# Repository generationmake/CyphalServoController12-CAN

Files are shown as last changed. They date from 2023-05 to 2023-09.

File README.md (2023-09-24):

# CyphalServoController12/CAN
Board to control up to 12 servos with a Raspberry Pi Pico to connect via CAN using OpenCyphal and UCANPHY Micro

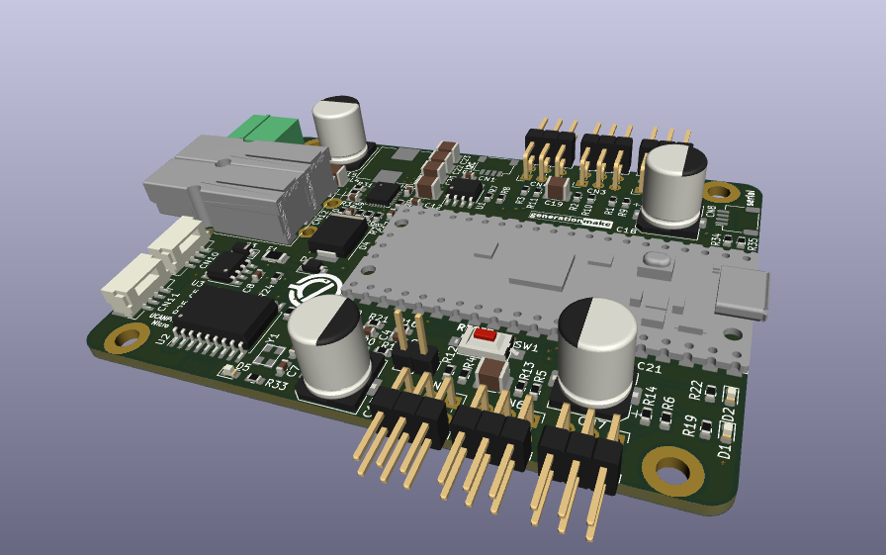
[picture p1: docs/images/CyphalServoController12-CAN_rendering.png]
CyphalServoController12/CAN rendering


## Description

### analog measurements

| **channel** | **usage** | **range**  |
|:---:|:---:|:---:|
| ADC0 | battery voltage | 0 - 66 V |
| ADC1 | servo voltage | 0 - 6.6 V  |
| ADC2 | CAN bus voltage | 0 - 6.6 V  |

### power supply

The power for the microcontroller and the CAN interface can be fed via the CAN connector or thepower regulator for the servos. The power regulator for the servos can be enabled and disabled by the microcontroller to save power in stand-by.

input voltage: 10 - 40 V

## PCB

### Top

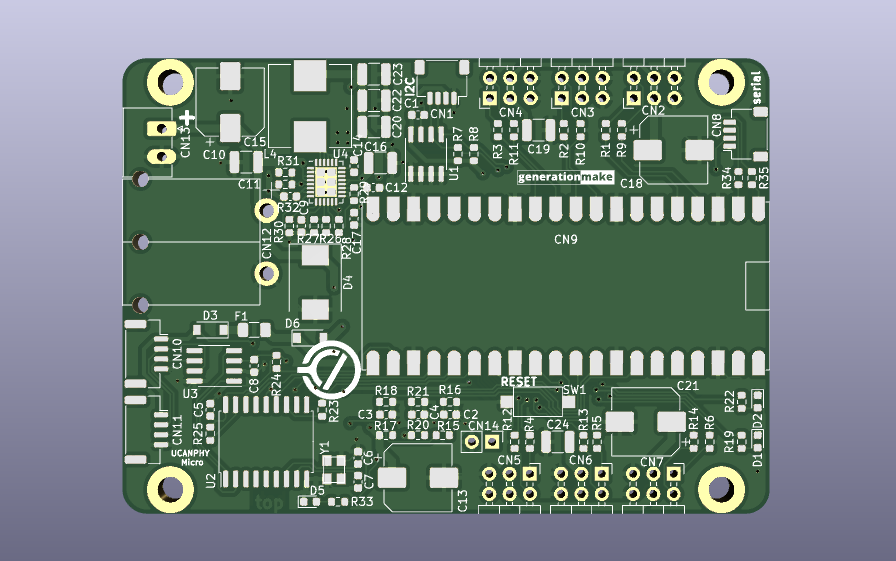
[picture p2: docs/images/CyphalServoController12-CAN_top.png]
CyphalServoController12/CAN PCB top


### Bottom

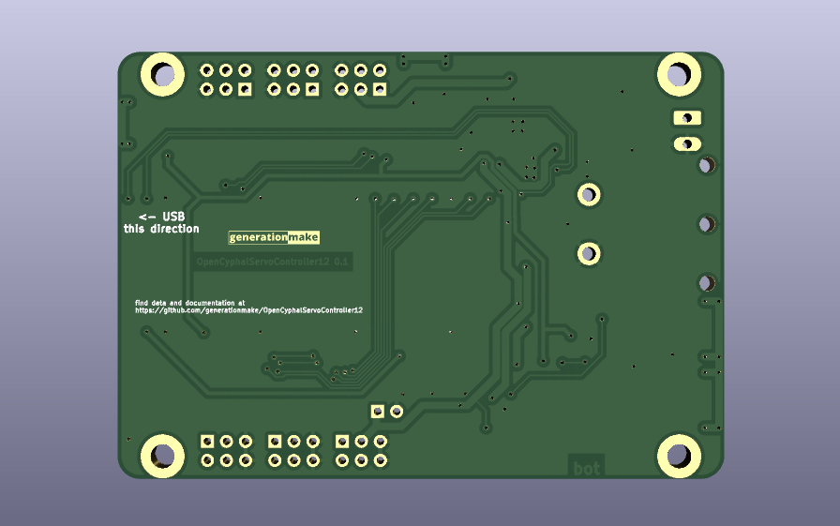
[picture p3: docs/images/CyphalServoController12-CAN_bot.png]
CyphalServoController12/CAN PCB bot


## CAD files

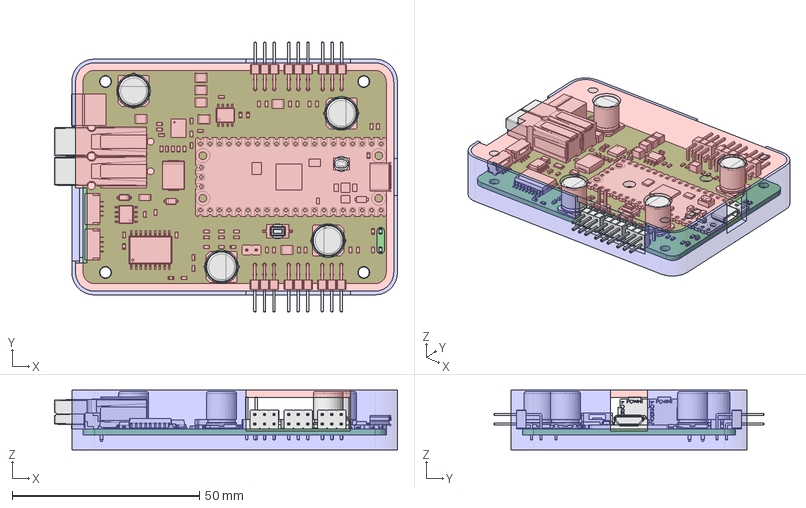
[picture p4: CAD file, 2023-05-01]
freecad_source/enclosure.FCStd
91.6 x 72.2 x 16.0 mm
bottom
top
OpenCyphalServoController12 PCB

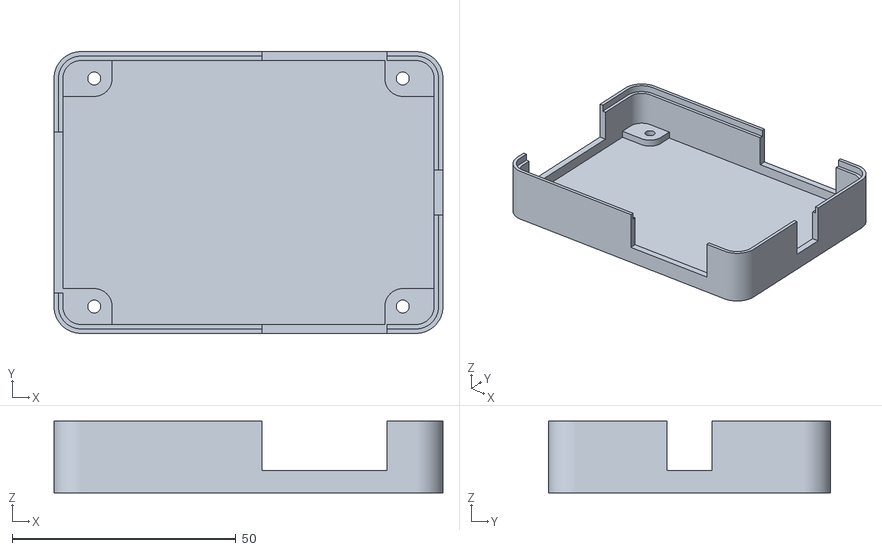
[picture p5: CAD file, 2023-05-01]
production_data/enclosure-bottom.stl
87.0 x 63.0 x 16.0

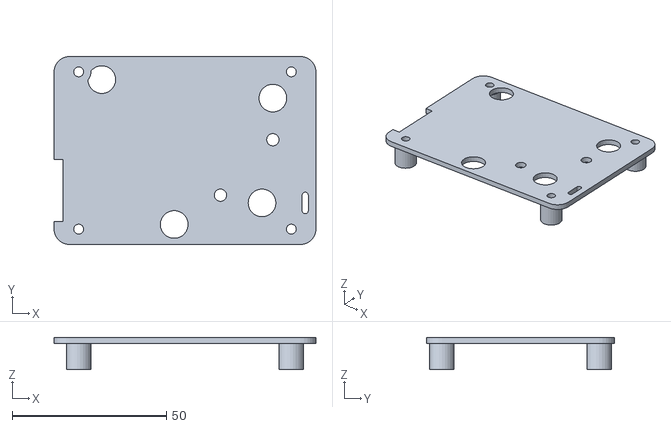
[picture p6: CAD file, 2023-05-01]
production_data/enclosure-top.stl
85.0 x 61.0 x 10.4

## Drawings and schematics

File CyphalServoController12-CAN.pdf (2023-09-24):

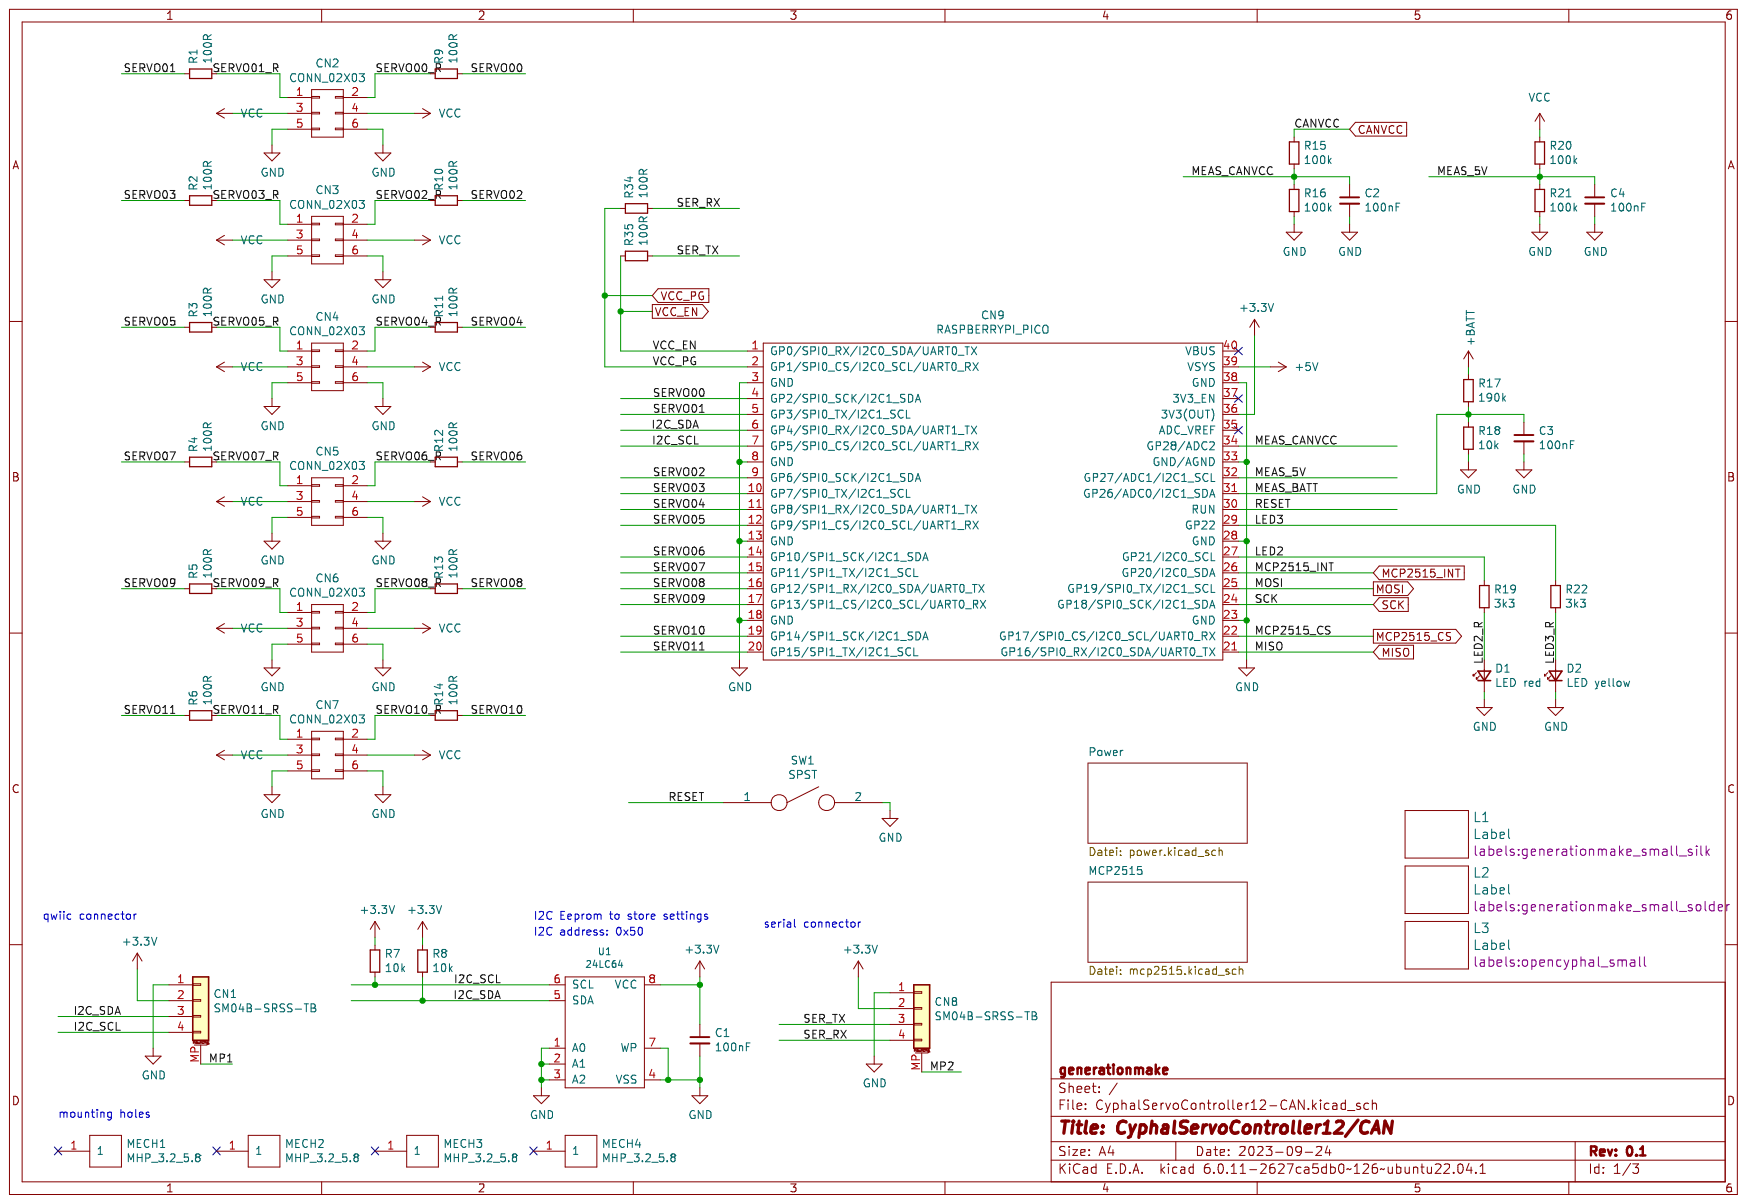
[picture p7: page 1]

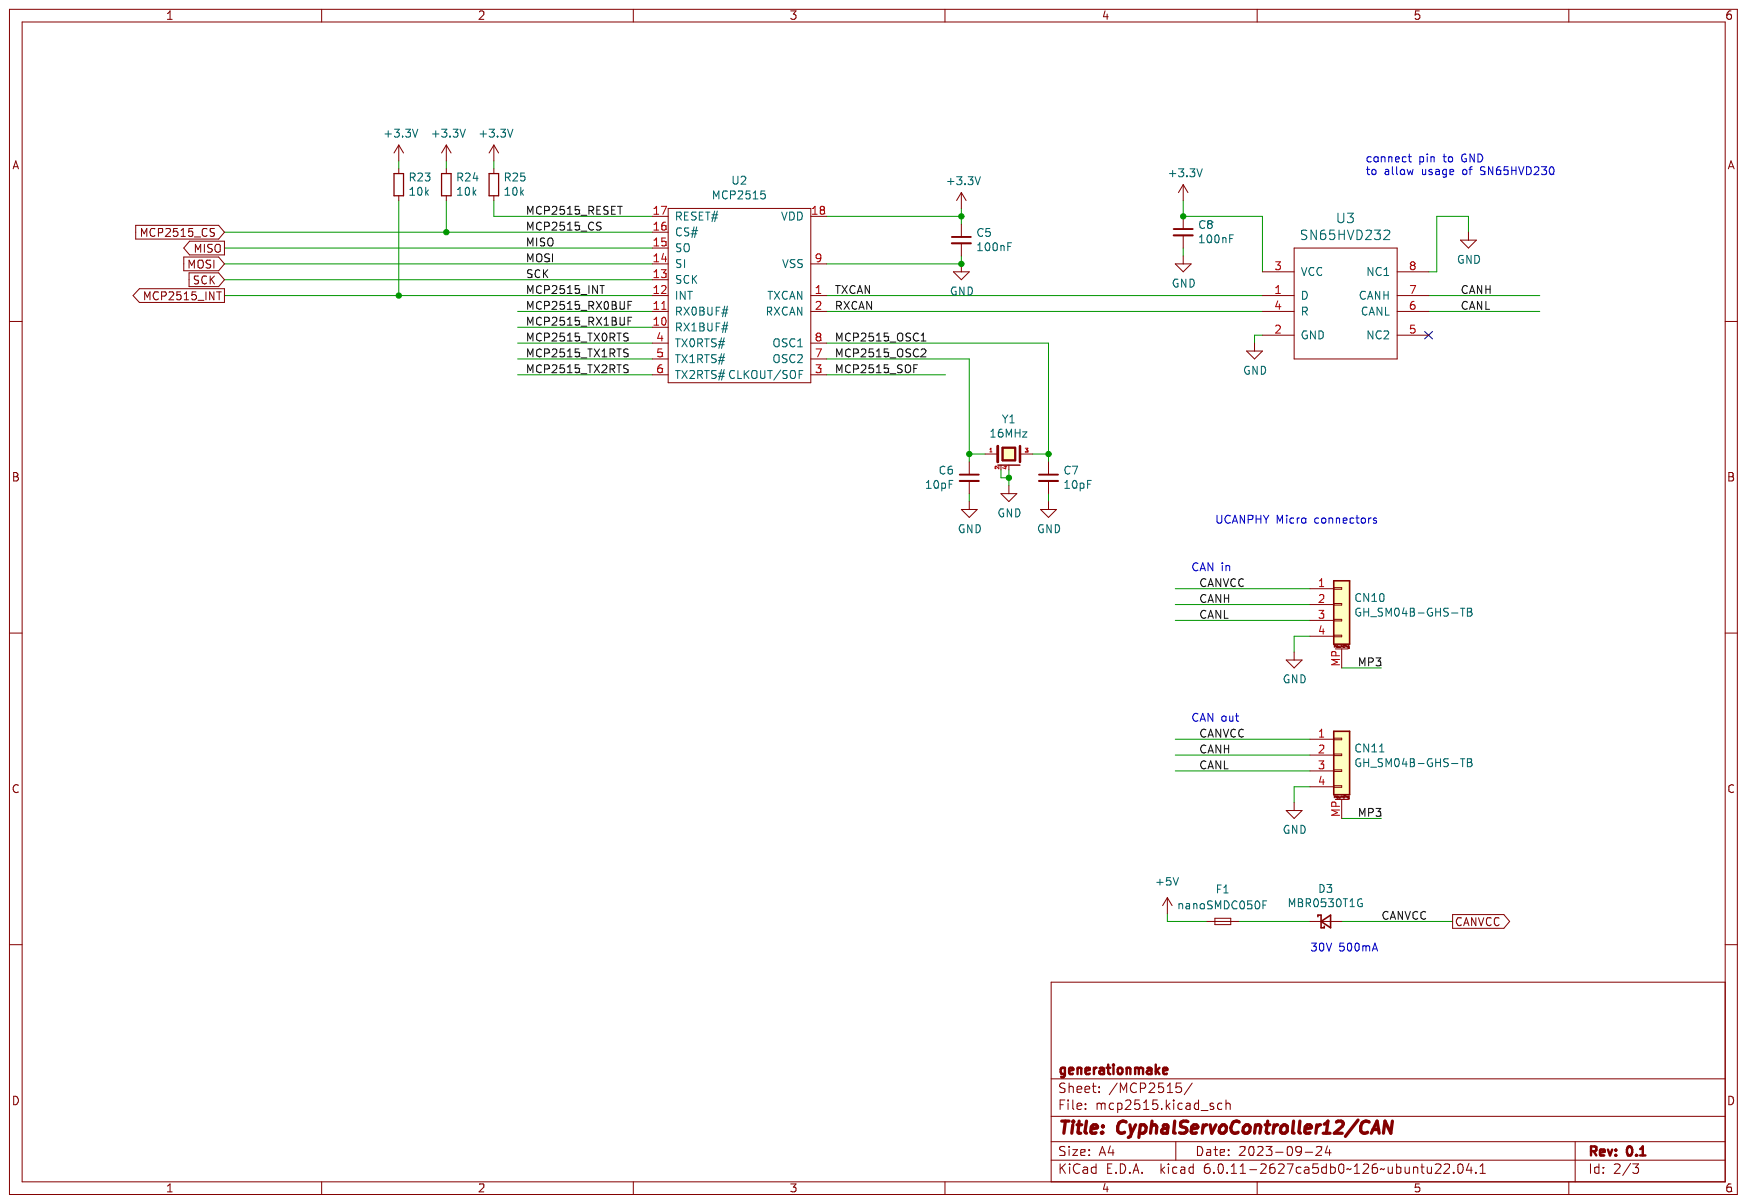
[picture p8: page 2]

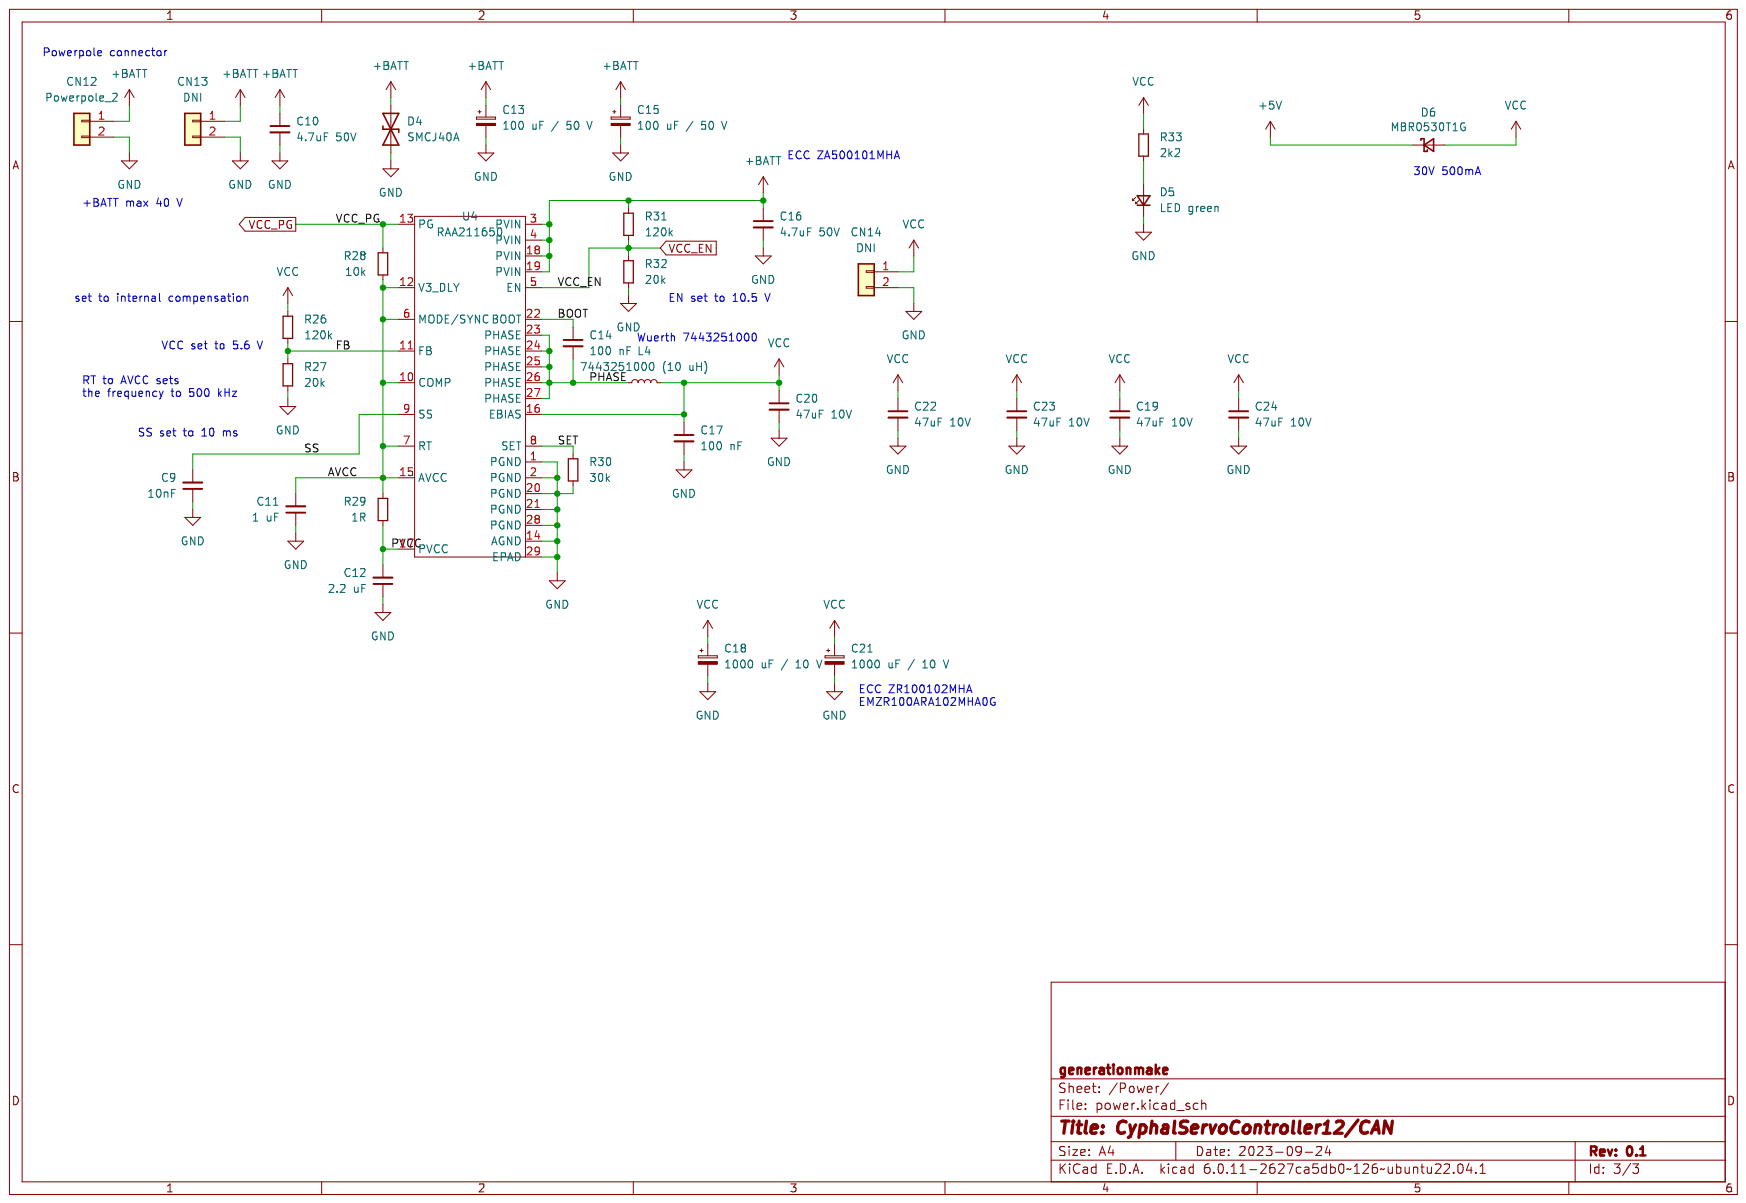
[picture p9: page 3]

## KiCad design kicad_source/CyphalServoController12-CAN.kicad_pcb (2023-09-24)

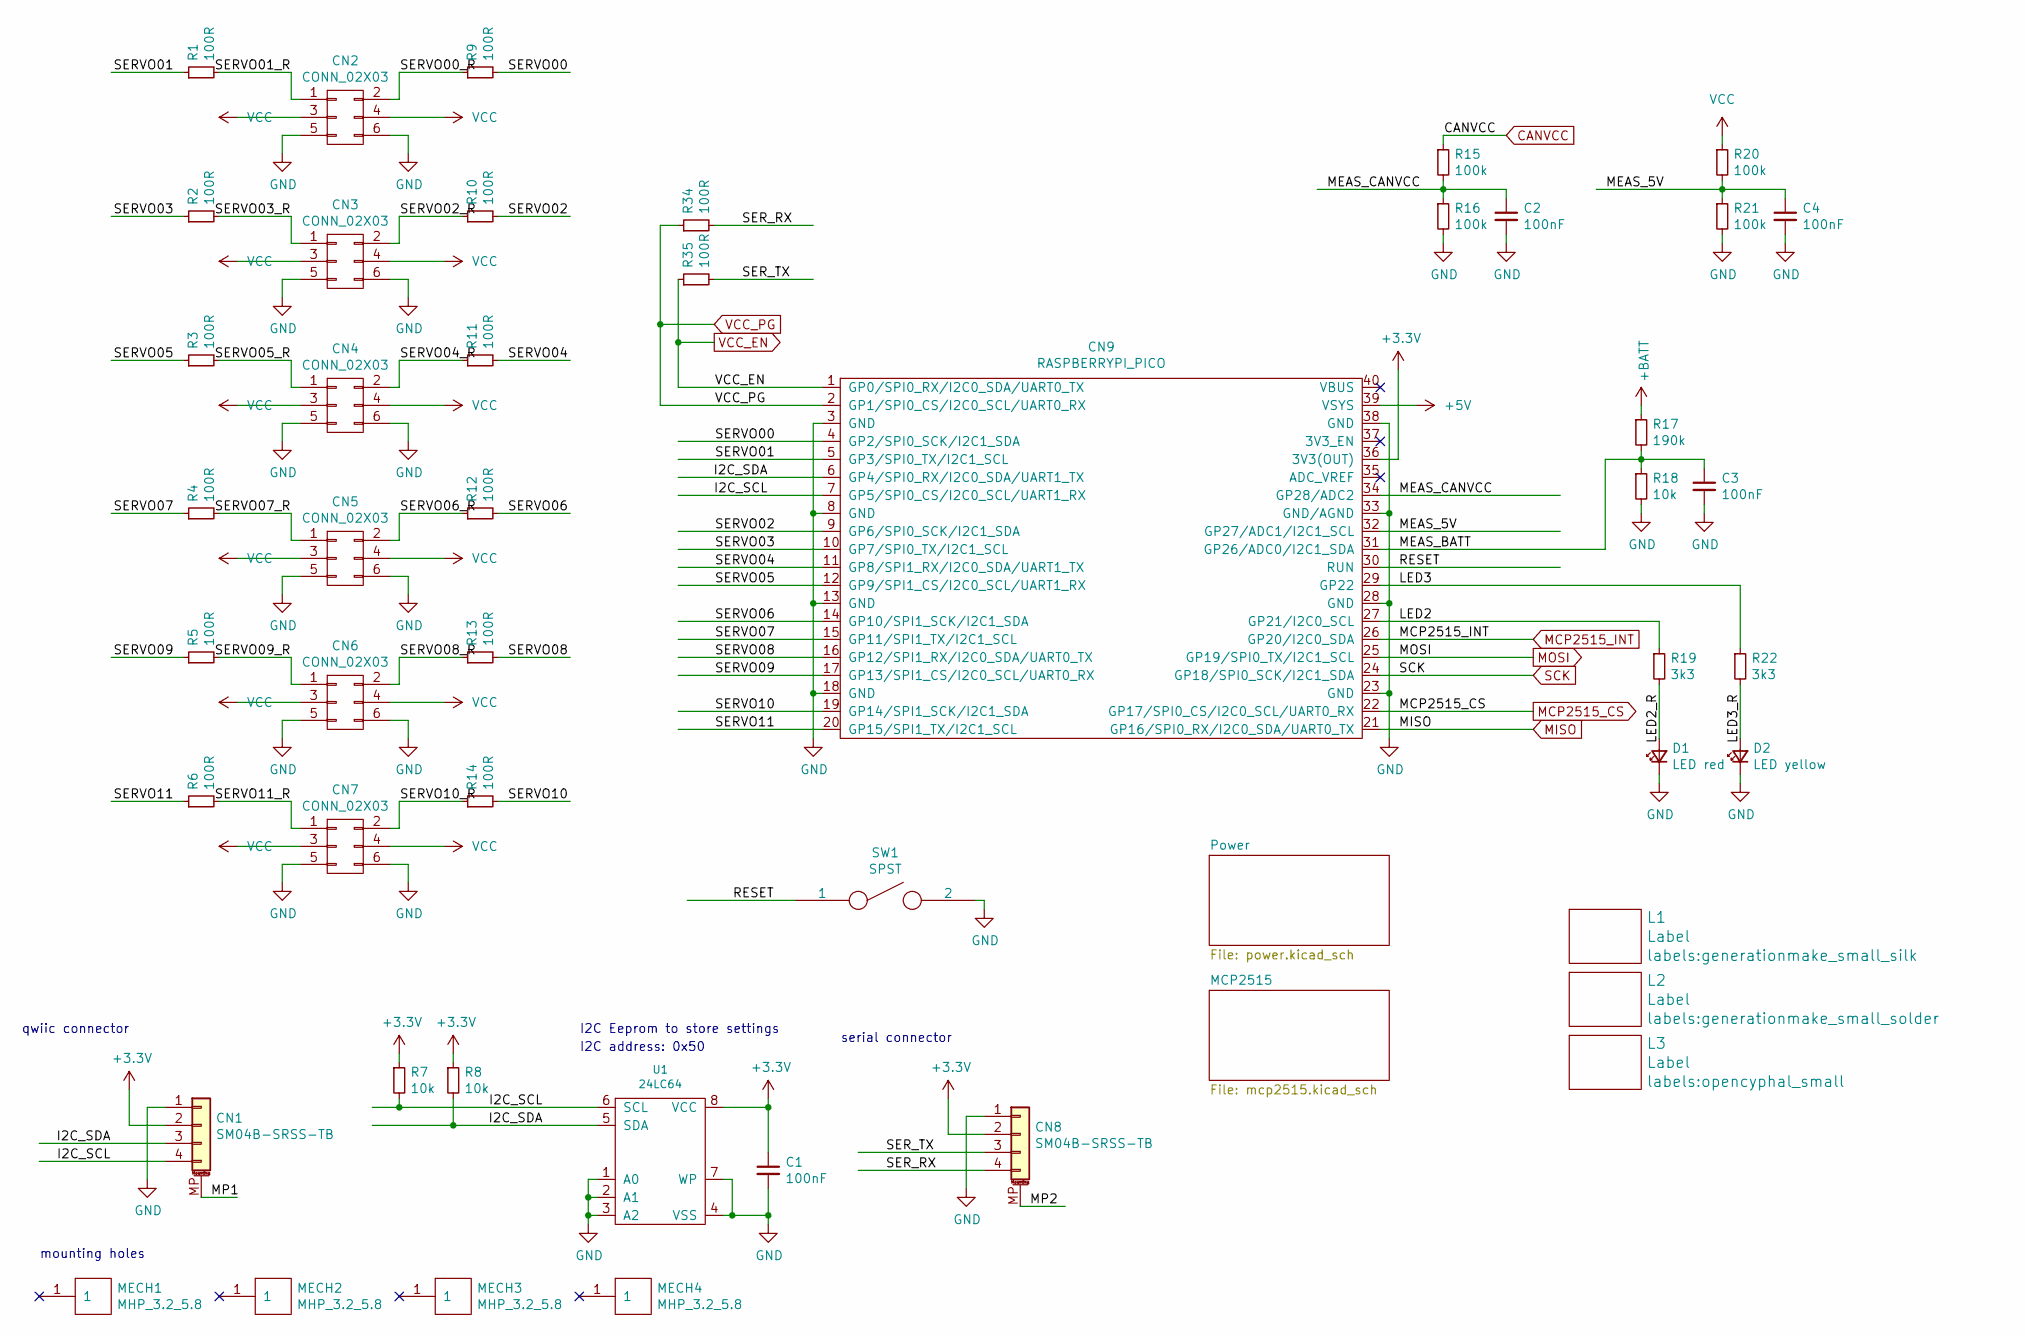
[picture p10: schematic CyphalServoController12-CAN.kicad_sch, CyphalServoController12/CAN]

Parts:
C1, C2, C3, C4: 100nF; C_0603_1608Metric
CN1, CN8: SM04B-SRSS-TB; JST_SH_SM04B-SRSS-TB_1x04-1MP_P1.00mm_Horizontal
CN2, CN3, CN4, CN5, CN6, CN7: CONN_02X03; PinHeader_2x03_P2.54mm_Horizontal
CN9: RASPBERRYPI_PICO; RASPI_PICO_SOLDER_Kopie
D1: LED red; LED_0603_1608Metric
D2: LED yellow; LED_0603_1608Metric
L1: Label; generationmake_small_silk
L2: Label; generationmake_small_solder
L3: Label; opencyphal_small
MECH1, MECH2, MECH3, MECH4: MHP_3.2_5.8
R1, R2, R3, R4, R5, R6, R9, R10, R11, R12, R13, R14, R34, R35: 100R; R_0603_1608Metric
R7, R8, R18: 10k; R_0603_1608Metric
R15, R16, R20, R21: 100k; R_0603_1608Metric
R17: 190k; R_0603_1608Metric
R19, R22: 3k3; R_0603_1608Metric
SW1: SPST; SW_SPST_CK_RS282G05A3
U1: 24LC64; SOIC-8_3.9x4.9mm_P1.27mm

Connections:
+3V3: C1.1, CN1.2, CN8.2, CN9.36 (3V3(OUT)), R7.1, R8.1, U1.8 (VCC); also elsewhere on the board
+5V: CN9.39 (VSYS); also elsewhere on the board
+BATT: R17.1; also elsewhere on the board
/I2C_SCL: CN1.4, CN9.7 (GP5/SPI0_CS/I2C0_SCL/UART1_RX), R7.2, U1.6 (SCL)
/I2C_SDA: CN1.3, CN9.6 (GP4/SPI0_RX/I2C0_SDA/UART1_TX), R8.2, U1.5 (SDA)
/LED2: CN9.27 (GP21/I2C0_SCL), R19.1
/LED2_R: D1.2 (A), R19.2
/LED3: CN9.29 (GP22), R22.1
/LED3_R: D2.2 (A), R22.2
/MEAS_5V: C4.1, CN9.32 (GP27/ADC1/I2C1_SCL), R20.2, R21.1
/MEAS_BATT: C3.1, CN9.31 (GP26/ADC0/I2C1_SDA), R17.2, R18.1
/MEAS_CANVCC: C2.1, CN9.34 (GP28/ADC2), R15.2, R16.1
/MP1: CN1.MP (MountPin)
/MP2: CN8.MP (MountPin)
/RESET: CN9.30 (RUN), SW1.1
/SERVO00: CN9.4 (GP2/SPI0_SCK/I2C1_SDA), R9.2
/SERVO00_R: CN2.2, R9.1
/SERVO01: CN9.5 (GP3/SPI0_TX/I2C1_SCL), R1.1
/SERVO01_R: CN2.1, R1.2
/SERVO02: CN9.9 (GP6/SPI0_SCK/I2C1_SDA), R10.2
/SERVO02_R: CN3.2, R10.1
/SERVO03: CN9.10 (GP7/SPI0_TX/I2C1_SCL), R2.1
/SERVO03_R: CN3.1, R2.2
/SERVO04: CN9.11 (GP8/SPI1_RX/I2C0_SDA/UART1_TX), R11.2
/SERVO04_R: CN4.2, R11.1
/SERVO05: CN9.12 (GP9/SPI1_CS/I2C0_SCL/UART1_RX), R3.1
/SERVO05_R: CN4.1, R3.2
/SERVO06: CN9.14 (GP10/SPI1_SCK/I2C1_SDA), R12.2
/SERVO06_R: CN5.2, R12.1
/SERVO07: CN9.15 (GP11/SPI1_TX/I2C1_SCL), R4.1
/SERVO07_R: CN5.1, R4.2
/SERVO08: CN9.16 (GP12/SPI1_RX/I2C0_SDA/UART0_TX), R13.2
/SERVO08_R: CN6.2, R13.1
/SERVO09: CN9.17 (GP13/SPI1_CS/I2C0_SCL/UART0_RX), R5.1
/SERVO09_R: CN6.1, R5.2
/SERVO10: CN9.19 (GP14/SPI1_SCK/I2C1_SDA), R14.2
/SERVO10_R: CN7.2, R14.1
/SERVO11: CN9.20 (GP15/SPI1_TX/I2C1_SCL), R6.1
/SERVO11_R: CN7.1, R6.2
/SER_RX: CN8.4, R34.2
/SER_TX: CN8.3, R35.2
CANVCC: R15.1; also elsewhere on the board
GND: C1.2, C2.2, C3.2, C4.2, CN1.1, CN2.5, CN2.6, CN3.5, CN3.6, CN4.5, CN4.6, CN5.5, CN5.6, CN6.5, CN6.6, CN7.5, CN7.6, CN8.1, CN9.3 (GND), CN9.8 (GND), CN9.13 (GND), CN9.18 (GND), CN9.23 (GND), CN9.28 (GND), CN9.33 (GND/AGND), CN9.38 (GND), D1.1 (K), D2.1 (K), R16.2, R18.2, R21.2, SW1.2, U1.1 (A0), U1.2 (A1), U1.3 (A2), U1.4 (VSS), U1.7 (WP); also elsewhere on the board
MCP2515_CS: CN9.22 (GP17/SPI0_CS/I2C0_SCL/UART0_RX); also elsewhere on the board
MCP2515_INT: CN9.26 (GP20/I2C0_SDA); also elsewhere on the board
MISO: CN9.21 (GP16/SPI0_RX/I2C0_SDA/UART0_TX); also elsewhere on the board
MOSI: CN9.25 (GP19/SPI0_TX/I2C1_SCL); also elsewhere on the board
SCK: CN9.24 (GP18/SPI0_SCK/I2C1_SDA); also elsewhere on the board
VCC: CN2.3, CN2.4, CN3.3, CN3.4, CN4.3, CN4.4, CN5.3, CN5.4, CN6.3, CN6.4, CN7.3, CN7.4, R20.1; also elsewhere on the board
VCC_EN: CN9.1 (GP0/SPI0_RX/I2C0_SDA/UART0_TX), R35.1; also elsewhere on the board
VCC_PG: CN9.2 (GP1/SPI0_CS/I2C0_SCL/UART0_RX), R34.1; also elsewhere on the board

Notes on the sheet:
serial connector
qwiic connector
mounting holes
I2C address: 0x50
I2C Eeprom to store settings

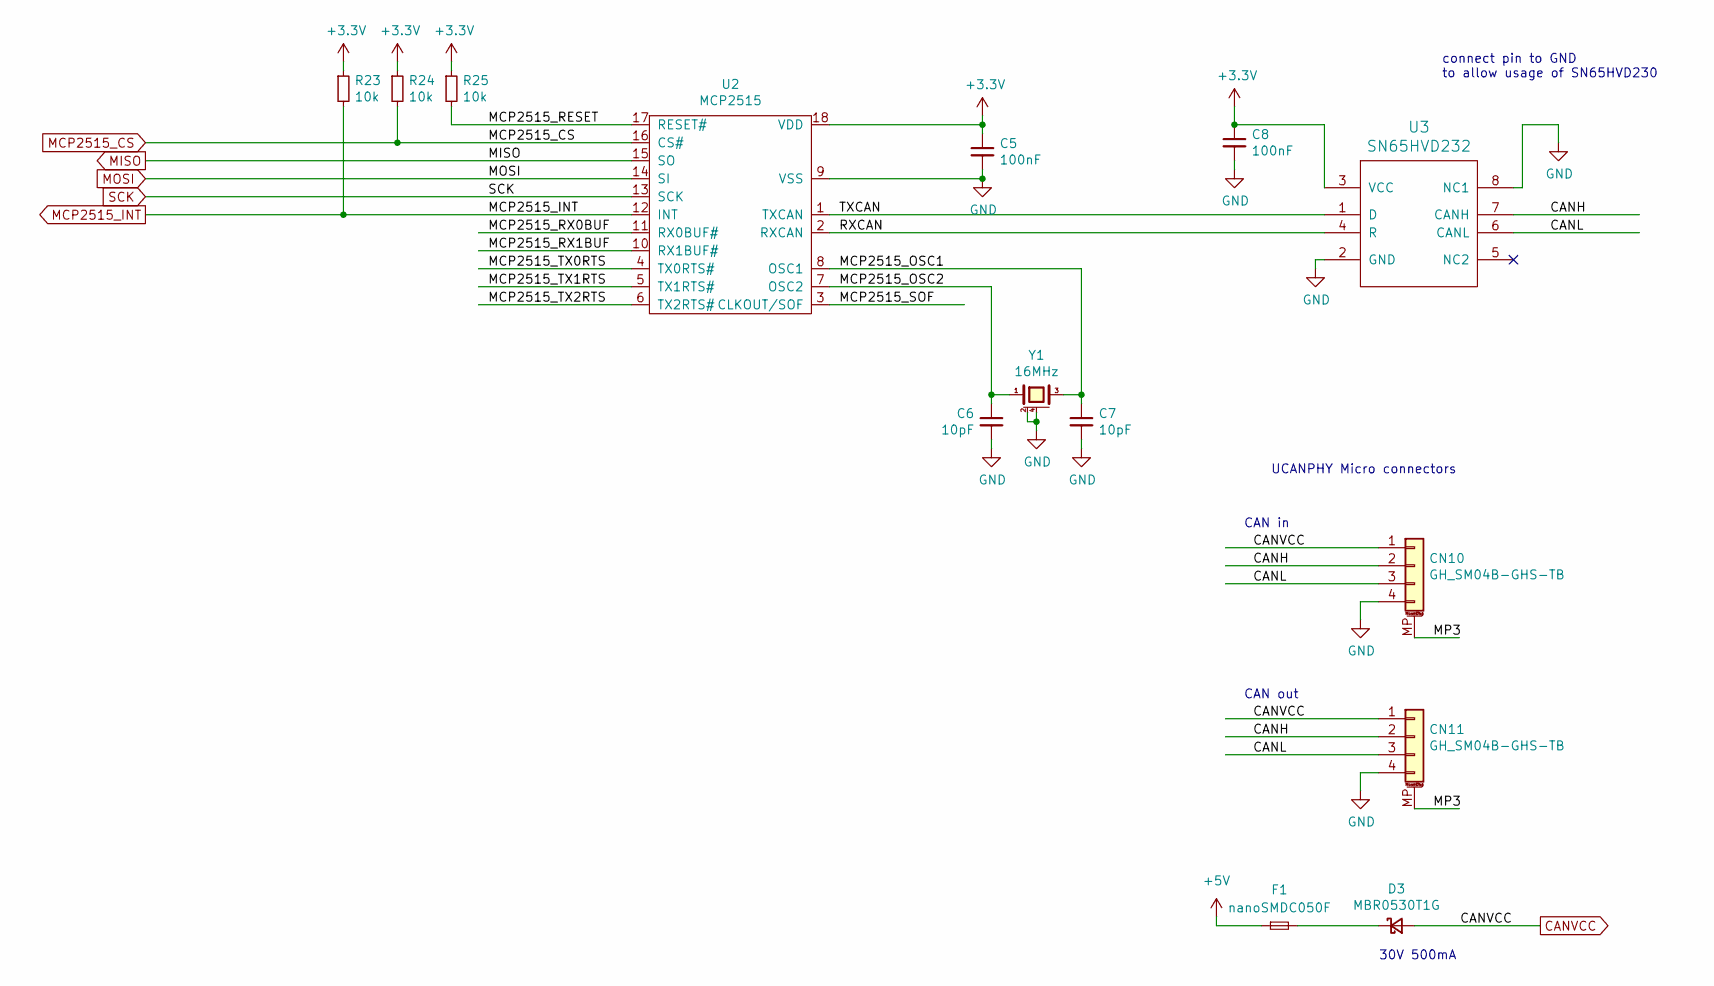
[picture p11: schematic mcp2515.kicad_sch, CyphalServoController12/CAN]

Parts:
C5, C8: 100nF; C_0603_1608Metric
C6, C7: 10pF; C_0603_1608Metric
CN10, CN11: GH_SM04B-GHS-TB; JST_GH_SM04B-GHS-TB_1x04-1MP_P1.25mm_Horizontal
D3: MBR0530T1G; D_SOD-123
F1: nanoSMDC050F; Fuse_1206_3216Metric
R23, R24, R25: 10k; R_0603_1608Metric
U2: MCP2515; SOIC-18W_7.5x11.6mm_P1.27mm
U3: SN65HVD232; SOIC-8_3.9x4.9mm_P1.27mm
Y1: 16MHz; Crystal_SMD_3.2x2.5mm_4Pad

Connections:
+3V3: C5.1, C8.1, R23.1, R24.1, R25.1, U2.18 (VDD), U3.3 (VCC); also elsewhere on the board
+5V: F1.1; also elsewhere on the board
/MCP2515/CANH: CN10.2, CN11.2, U3.7 (CANH)
/MCP2515/CANL: CN10.3, CN11.3, U3.6 (CANL)
/MCP2515/MCP2515_OSC1: C7.1, U2.8 (OSC1), Y1.3
/MCP2515/MCP2515_OSC2: C6.1, U2.7 (OSC2), Y1.1
/MCP2515/MCP2515_RESET: R25.2, U2.17 (RESET#)
/MCP2515/MCP2515_RX0BUF: U2.11 (RX0BUF#)
/MCP2515/MCP2515_RX1BUF: U2.10 (RX1BUF#)
/MCP2515/MCP2515_SOF: U2.3 (CLKOUT/SOF)
/MCP2515/MCP2515_TX0RTS: U2.4 (TX0RTS#)
/MCP2515/MCP2515_TX1RTS: U2.5 (TX1RTS#)
/MCP2515/MCP2515_TX2RTS: U2.6 (TX2RTS#)
/MCP2515/MP3: CN10.MP (MountPin), CN11.MP (MountPin)
/MCP2515/RXCAN: U2.2 (RXCAN), U3.4 (R)
/MCP2515/TXCAN: U2.1 (TXCAN), U3.1 (D)
CANVCC: CN10.1, CN11.1, D3.2 (A); also elsewhere on the board
GND: C5.2, C6.2, C7.2, C8.2, CN10.4, CN11.4, U2.9 (VSS), U3.2 (GND), U3.8 (NC1), Y1.2 (case), Y1.4 (case); also elsewhere on the board
MCP2515_CS: R24.2, U2.16 (CS#); also elsewhere on the board
MCP2515_INT: R23.2, U2.12 (INT); also elsewhere on the board
MISO: U2.15 (SO); also elsewhere on the board
MOSI: U2.14 (SI); also elsewhere on the board
unnamed: D3.1 (K), F1.2
SCK: U2.13 (SCK); also elsewhere on the board

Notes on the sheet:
connect pin to GND to allow usage of SN65HVD230
UCANPHY Micro connectors
30V 500mA
CAN in
CAN out

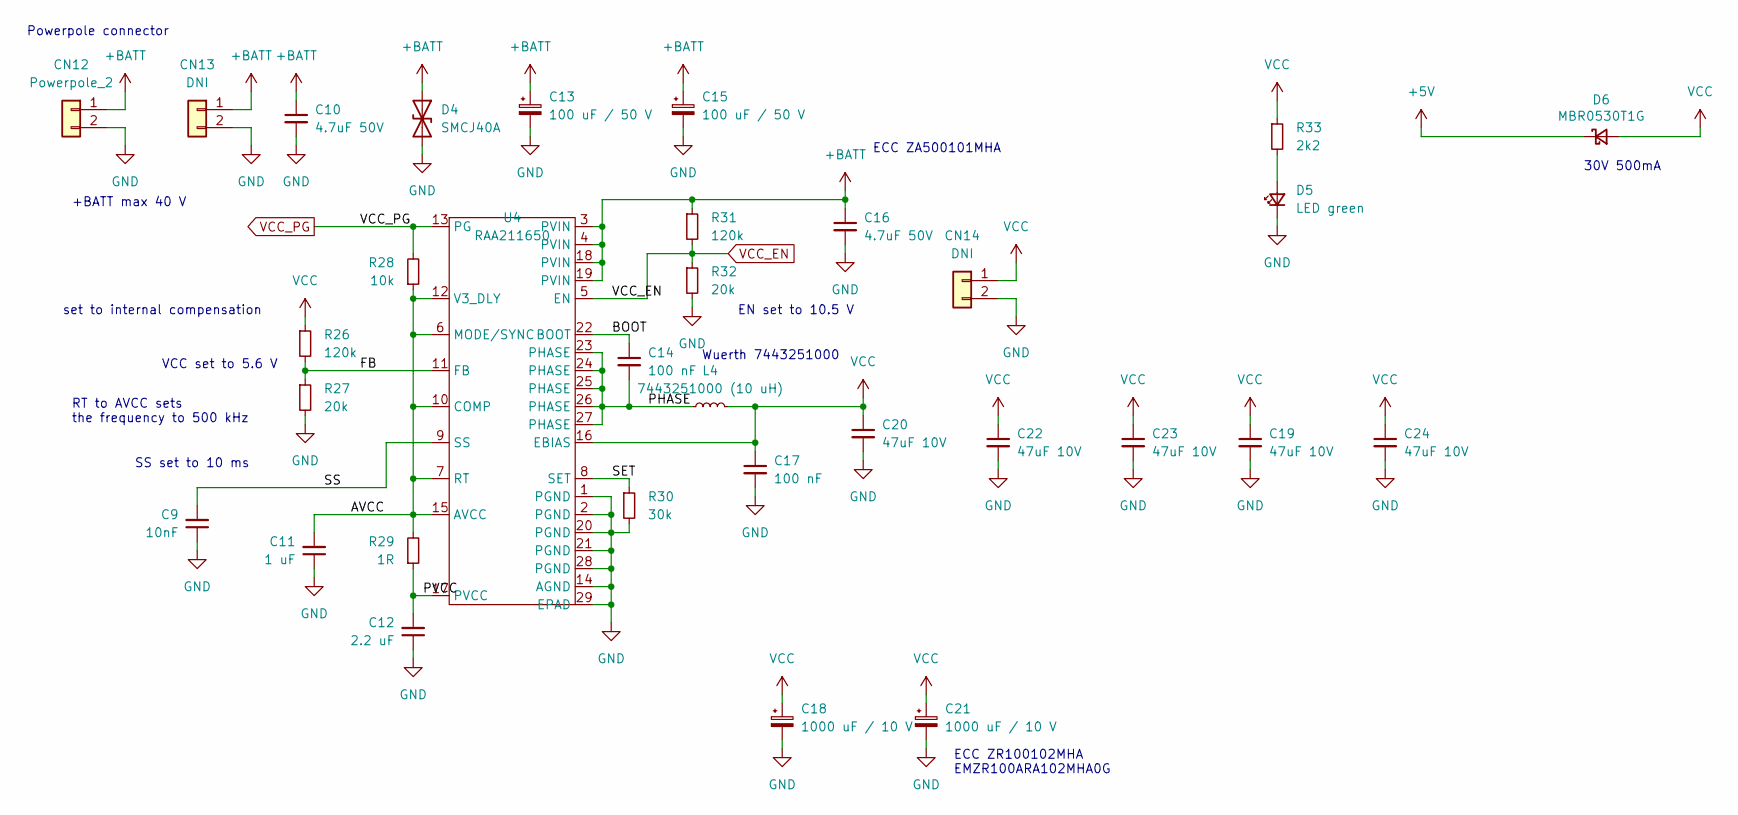
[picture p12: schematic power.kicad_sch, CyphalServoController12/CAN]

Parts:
C9: 10nF; C_0603_1608Metric
C10, C16: 4.7uF 50V; C_1210_3225Metric
C11: 1 uF; C_0603_1608Metric
C12: 2.2 uF; C_0603_1608Metric
C13, C15: 100 uF / 50 V; CP_Elec_8x10
C14, C17: 100 nF; C_0603_1608Metric
C18, C21: 1000 uF / 10 V; CP_Elec_8x10
C19, C20, C22, C23, C24: 47uF 10V; C_1210_3225Metric
CN12: Powerpole_2; POWERPOLE_hor_2
CN13: DNI; PhoenixContact_MC_1,5_2-G-3.5_1x02_P3.50mm_Horizontal
CN14: DNI; PinHeader_1x02_P2.54mm_Vertical
D4: SMCJ40A; D_SMC
D5: LED green; LED_0603_1608Metric
D6: MBR0530T1G; D_SOD-123
L4: 7443251000 (10 uH); L_Wuerth_HCI-1050
R26, R31: 120k; R_0603_1608Metric
R27, R32: 20k; R_0603_1608Metric
R28: 10k; R_0603_1608Metric
R29: 1R; R_0603_1608Metric
R30: 30k; R_0603_1608Metric
R33: 2k2; R_0603_1608Metric
U4: RAA211650; QFN-28-1EP_4x5mm_P0.5mm_EP2.65x3.65mm

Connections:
+5V: D6.1 (K); also elsewhere on the board
+BATT: C10.1, C13.1, C15.1, C16.1, CN12.1, CN13.1, D4.1 (A1), R31.1, U4.3 (PVIN), U4.4 (PVIN), U4.18 (PVIN), U4.19 (PVIN); also elsewhere on the board
/Power/AVCC: C11.2, R28.1, R29.2, U4.6 (MODE/SYNC), U4.7 (RT), U4.10 (COMP), U4.12 (V3_DLY), U4.15 (AVCC)
/Power/BOOT: C14.1, U4.22 (BOOT)
/Power/FB: R26.2, R27.1, U4.11 (FB)
/Power/PHASE: C14.2, L4.1, U4.23 (PHASE), U4.24 (PHASE), U4.25 (PHASE), U4.26 (PHASE), U4.27 (PHASE)
/Power/PVCC: C12.2, R29.1, U4.17 (PVCC)
/Power/SET: R30.1, U4.8 (SET)
/Power/SS: C9.2, U4.9 (SS)
GND: C9.1, C10.2, C11.1, C12.1, C13.2, C15.2, C16.2, C17.2, C18.2, C19.2, C20.2, C21.2, C22.2, C23.2, C24.2, CN12.2, CN13.2, CN14.2, D4.2 (A2), D5.1 (K), R27.2, R30.2, R32.2, U4.1 (PGND), U4.2 (PGND), U4.14 (AGND), U4.20 (PGND), U4.21 (PGND), U4.28 (PGND), U4.29 (EPAD); also elsewhere on the board
unnamed: D5.2 (A), R33.2
VCC: C17.1, C18.1, C19.1, C20.1, C21.1, C22.1, C23.1, C24.1, CN14.1, D6.2 (A), L4.2, R26.1, R33.1, U4.16 (EBIAS); also elsewhere on the board
VCC_EN: R31.2, R32.1, U4.5 (EN); also elsewhere on the board
VCC_PG: R28.2, U4.13 (PG); also elsewhere on the board

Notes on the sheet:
Wuerth 7443251000
EN set to 10.5 V
+BATT max 40 V
ECC ZR100102MHA EMZR100ARA102MHA0G
set to internal compensation
ECC ZA500101MHA
RT to AVCC sets the frequency to 500 kHz
30V 500mA
VCC set to 5.6 V
Powerpole connector
SS set to 10 ms

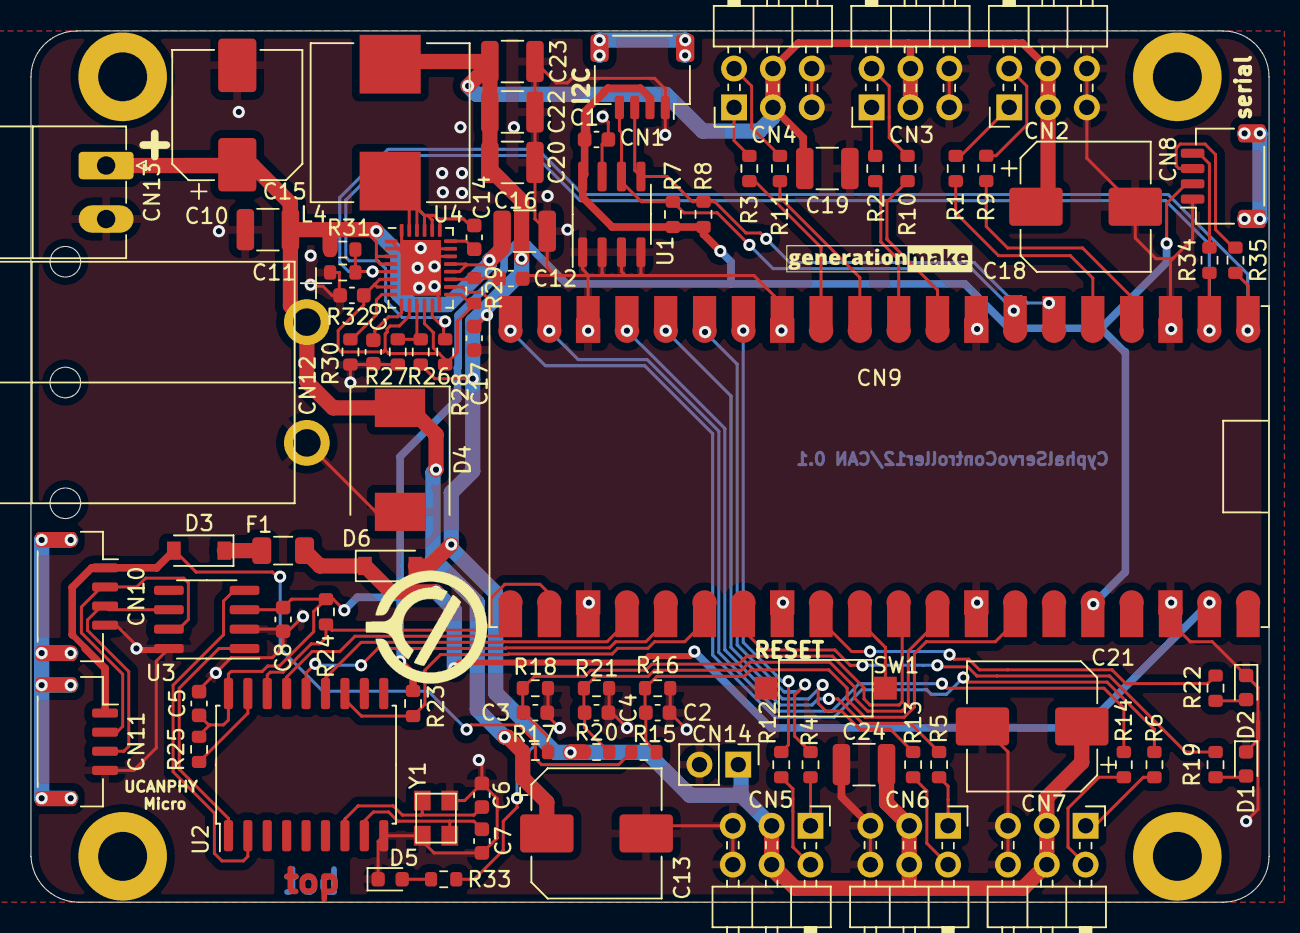
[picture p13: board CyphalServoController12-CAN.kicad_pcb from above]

Board: 2 copper layers, 81.0 x 57.0 mm, 94 parts (1 on the bottom side), 66 nets.

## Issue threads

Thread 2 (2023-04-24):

[Feature Request] Please design 3D printed case

aentinger, 2023-04-24:

aentinger, 2023-09-22:
Fixed by #4 .

Closed 2023-09-22.

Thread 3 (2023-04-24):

[Feature Request] Consider voltage level conversion for PWM output

aentinger, 2023-04-24:
Currently the PWM output is at 3V3. But most servos are powered with 5 - 6V. While this may work its not a clean solution, as the PWM signal level should match the supply voltage level.

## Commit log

2023-03-26 updated some labels
    [OpenCyphalServoController12.kicad_pcb]
2023-05-01 generated step file
    [OpenCyphalServoController12.kicad_pcb]
2023-05-01 added freecad project
    [enclosure.FCStd]
2023-05-01 generated stl files for production
    [enclosure-bottom.stl, enclosure-top.stl]
2023-09-23 renamed files
    [CyphalServoController12-CAN.kicad_pcb, CyphalServoController12-CAN.kicad_sch]
2023-09-23 renamed comments and labels in kicad project
    [CyphalServoController12-CAN.kicad_pcb, CyphalServoController12-CAN.kicad_sch, mcp2515.kicad_sch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]
